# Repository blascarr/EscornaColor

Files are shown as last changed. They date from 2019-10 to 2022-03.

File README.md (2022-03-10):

# EscornaColor
Version de Escornabot con sensor de color **TCS3200**.

El **sensor de color TCS3200** añade formatos de juego interesantes al famoso modelo de [**Escornabot**](https://escornabot.com/web/es).

Para usar el sensor de color, es necesario sustituir la pieza del alojamiento para la canica con el siguiente [modelo STL](https://www.thingiverse.com/thing:3934783) publicado en [Thingiverse](https://www.thingiverse.com/thing:3934783).

<p align="center">
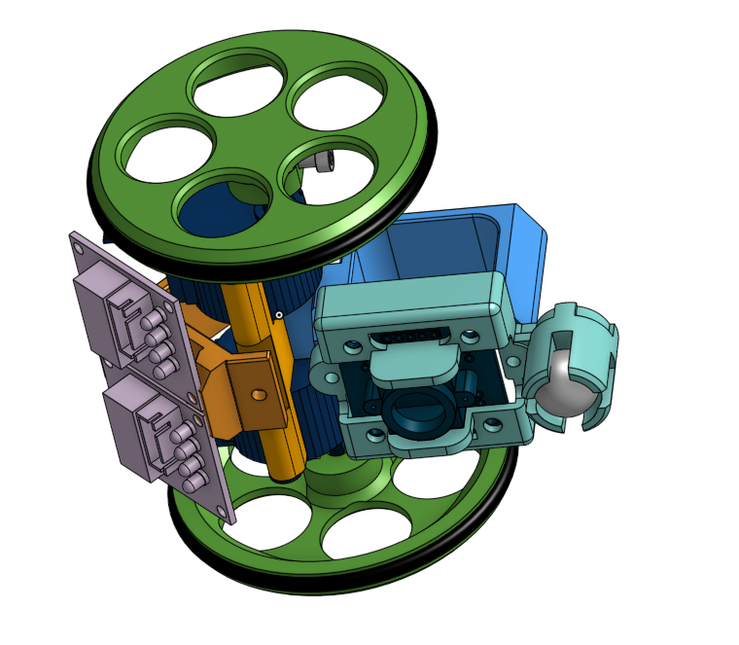
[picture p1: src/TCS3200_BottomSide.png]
	
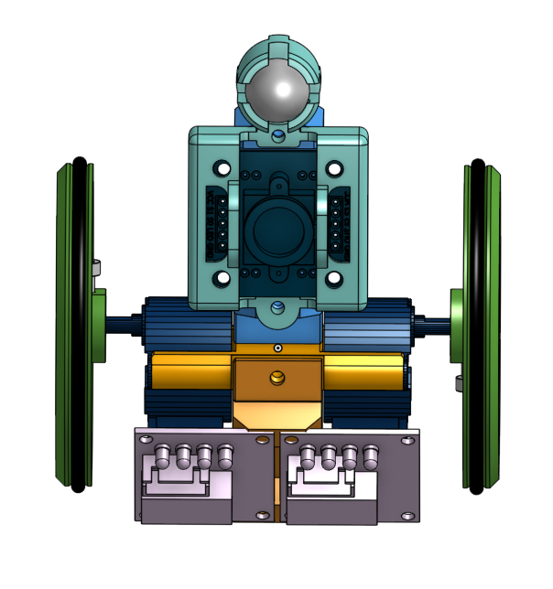
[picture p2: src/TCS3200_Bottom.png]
	
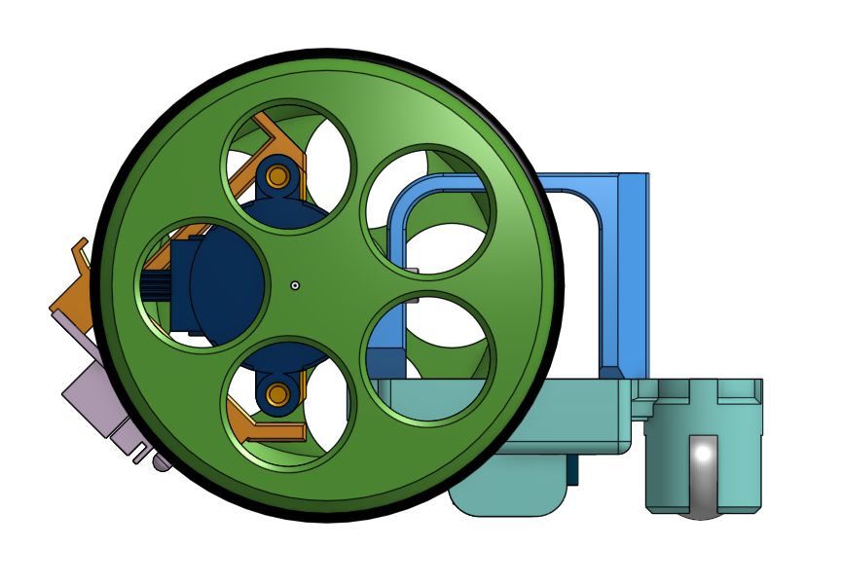
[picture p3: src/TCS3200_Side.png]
	
</p>

El sensor tiene distintos pines, de los cuales los más importantes son el pin S2, S3 y OUT. El pin de LED nos servirá solamente para encender y apagar el módulo.
- S2 --> D11
- S3 --> D12
- OUT --> D13
- LED --> A6
- S0 --> VCC
- S1 --> VCC

Este sensor de color viene preparado para reconocer **8 colores** por defecto que son:

- BLANCO
- NEGRO
- ROJO
- VERDE
- AZUL
- AMARILLO
- NARANJA
- MARRON

# Programa tu EscornaColor.

Para desarrollar una programación personalizada de tu EscornaColor, solo tienes que registrar una función a cada movimiento y **programar tu robot con tus propias reglas**.

Te dejamos unos códigos de ejemplo para que puedas crear tu propio modelo de programación.

Existen dos funciones en caso de ganar ( **win()** ) y en caso de perder el juego ( **game_over()** ).
Puedes crear un modelo de juego en el que puedes perder vidas en función del color que el **EscornaColor** ha detectado. Si el **EscornaColor** llega al color objetivo sin perder todas las vidas ganas.
```cpp
Bot ESCORNABOT;
int lives = 2;

void red(){
  ESCORNABOT.win();
}

void green(){
  lives -= 1;
  Serial.print("Lives: ");Serial.println(lives);
  if (lives <= 0 ){
    ESCORNABOT.game_over();
    Serial.println("GAME OVER");
  }
}
```

También puedes programar los movimientos en función del color que has encontrado con la función **move( )**. Dentro del parámetro de esta función puedes definir los siguientes tipos de movimiento.

- MOVE_NONE
- MOVE_FORWARD
- MOVE_RIGHT
- MOVE_BACKWARD
- MOVE_LEFT
- MOVE_PAUSE
- MOVE_ALT_RIGHT
- MOVE_ALT_LEFT

```cpp
void white(){
  ESCORNABOT.move( MOVE_BACKWARD );
  Serial.println("COLOR White");
}

void black(){
  ESCORNABOT.move( MOVE_FORWARD );
  Serial.println("COLOR Black");
}
```
Ten cuidado, porque puedes caer facilmente en un bucle de movimientos si no piensas bien la secuencia.

Una vez finalizadas tus reglas de juego, deberás asociar una accion de color a cada color en el **setup** de tu programa. El bucle loop se encargará de todo-

```cpp
void setup()
{
    ESCORNABOT.init();
    ESCORNABOT.load_colortable();

    //Color Actions Define
    ESCORNABOT.color_action( WHITE , white );
    ESCORNABOT.color_action( BLACK , black );
    ESCORNABOT.color_action( RED , red );
    
    //GREEN change non consecutively
    ESCORNABOT.color_action( GREEN , green, true );
    //YELLOW need to change from consecutive yellow colors
    ESCORNABOT.color_action( YELLOW , yellow );
    
    //random movements for Blue color
    randomSeed(analogRead(5));
    ESCORNABOT.color_action( BLUE , blue );

    //Brown and Orange not working
    ESCORNABOT.color_action( BROWN , aux_void );
    ESCORNABOT.color_action( ORANGE , aux_void );
}

void loop()
{
    ESCORNABOT.loop();
}

//Auxiliar void function for every color action defined
void aux_void(){
  
}
```

Al final, solo tienes que cargar el código a tu robot y dejarlo funcionar con los objetivos que te has definido.

**IMPORTANTE:** Ten cuidado de no saturar la memoria. Si superas más del 85% de la memoria RAM pueden ocurrir errores, pero puedes jugártela. 

# Formatos de juego a desarrollar.

- [x] El **EscornaColor** tiene un número de vidas limitado. Los colores pueden quitar vidas. El objetivo es llegar vivo al objetivo.
- [ ] Cuando se alcanza un color, se ejecutan las acciones de movimiento hasta llegar al objetivo. Juego de la hormiga. [Hormiga de Langton Simplificado](https://es.wikipedia.org/wiki/Hormiga_de_Langton)

- [ ] A través de una aplicación se pueden ver los colores y movimientos del Escornabot. Sin mirar el tablero ni al EscornaColor hay que dibujar el tablero original.

- [ ] Programación libre de escornabot con distintas dinámicas en base a las lecturas del sensor de color.

El sensor de color requiere de una **calibración inicial** para poder clasificar los colores correctamente. 

# [Calibración del sensor de color TCS3200](http://blascarr.com/lessons/tcs3200-color-sensor-calibration/)

El **Escornacolor** está configurado por defecto para cargar la calibración almacenada en la **EEPROM** manteniendo presionado el botón delantero.

De la misma forma, el **Escornacolor** realizará una calibración manteniendo presionado el botón trasero.

Para realizar esta calibración hay que acceder al puerto serie y escribir un caracter **Y** o **N** para que vaya realizando calibraciones.
En cada calibración nos preguntarán si queremos guardar nuestra tabla de colores en la **EEPROM**. 

Esta calibración se puede realizar a través del **monitor serie** o por **Bluetooth** a través de una aplicación.

### Calibración de intensidades BLANCO - NEGRO
Primero hay que calibrar las lecturas con respecto el color negro **BLACK CALIBRATION** y al color blanco **WHITE CALIBRATION**, que establecen los límites de lectura del sensor. Esta calibración es muy importante para la calibración de nuestra **tabla de colores**. 

### Calibración de la **tabla de colores**
Acto seguido se requiere de una calibración de una tabla de **8 colores** que se almacenan en la **memoria EEPROM**.

Los dos primeros colores son el color **Blanco** y el color **Negro**, y las lecturas deben corresponder a los valores RGB **( 255, 255, 255 )** y **( 0, 0, 0 )** respectivamente.

El resto de colores será una combinación de estos valores RGB. 
**NOTA:** Los valores RGB de cada color debida a la calibración no tienen por qué corresponder exactamente con los valores RGB del color. Esta calibración es una aproximación para cada medida.

# Añade más colores a tu EscornaColor

WORK IN PROGRESS.

Se pueden añadir más colores, pero para ello, hay que tener en cuenta que exista una variación notable en las lecturas para colores .
Recomendamos utilizar variantes de colores facilmente diferenciables, ya que tonos similares pueden dar lugar a errores.

Por ejemplo, el blanco y el amarillo son muy similares. Si la lectura se hace en un punto medio entre dos colores, el resultado puedes ser indeterminado.

Esta extensión se basa en el desarrollo de una librería para módulos **TCS3200** accesible en el siguiente [enlace](https://github.com/blascarr/TCS3200-ColorSensor).

- Puedes aprender más sobre el color en esta [Introducción al color en robótica](http://blascarr.com/lessons/introduccion-al-color/)

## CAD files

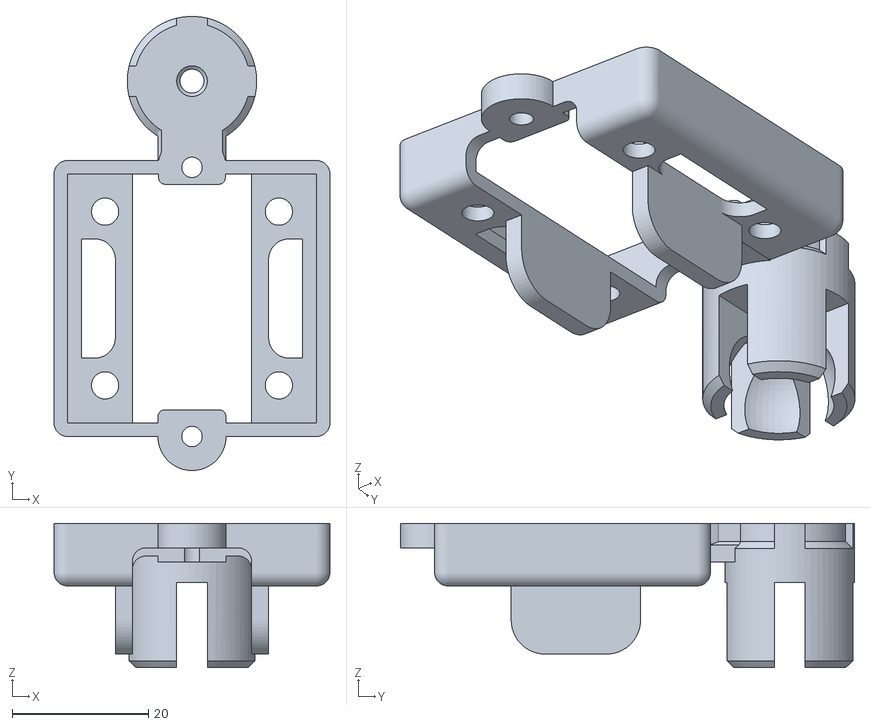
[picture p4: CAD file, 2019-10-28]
STL/ColorSensor_Escornabot.stl
40.5 x 66.6 x 21.2

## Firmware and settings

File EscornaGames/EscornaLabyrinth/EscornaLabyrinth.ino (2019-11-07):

// Escornabot.ino

#include "Bot.h"

//////////////////////////////////////////////////////////////////////
/*
  Reglas del juego.

  Nuestro robot debe ir desde la casilla de color naranja, hasta la casilla de color Verde.
  Pero el tablero aún no está construido completamente. 
  Solo hay unas cuantas casillas que son las trampas que deberemos evitar.
  El resto de colores tienen programados diferentes movimientos.
  Nuestra misión es descubrir que movimiento se corresponde con cada color para llegar desde la salida hasta la meta de forma directa.

  Os dejamos un ejemplo de tablero 

  ////////////////////////////////////////////////////
  |       |       |       |       |       |       |
  |       |       |       |       |       |       |
  |       |       |       |       |       |       |
  ////////////////////////////////////////////////////
  |       |       |       |       |       |       |
  |       |       |   R   |       |   R   |   V   | (META)
  |       |       |       |       |       |       |
  ////////////////////////////////////////////////////  
  |       |       |       |       |       |       |
  |       |   R   |       |       |   R   |       |
  |       |       |       |       |       |       |
  ////////////////////////////////////////////////////
  |       |       |       |       |       |       |
  |SALIDA |       |       |       |       |       |
  |       |       |       |       |       |       |
  ////////////////////////////////////////////////////
  /
*/

Bot ESCORNABOT;
int lives = 4;


void leftforward(){
  ESCORNABOT.move( MOVE_FORWARD );
  ESCORNABOT.move( MOVE_LEFT );
  Serial.println("LEFT - FORWARD");
}

void rightforward(){
  ESCORNABOT.move( MOVE_BACKWARD );
  ESCORNABOT.move( MOVE_RIGHT );
  Serial.println("LEFT - RIGHT");
}

void forward(){
  ESCORNABOT.move( MOVE_FORWARD );
  Serial.println("FORWARD");
}

void winner(){
  ESCORNABOT.win();
  Serial.println(" YOU WIN ");
}

void randomMove(){
    ESCORNABOT.move( random( 8 ) );
    Serial.println(" RANDOM MOVE ");
}

void warning(){
    damage();
    randomMove();
    
}

void damage(){
  lives -= 1;
  Serial.print("Lives: ");Serial.println(lives);
  if (lives <= 0 ){
    ESCORNABOT.game_over();
    Serial.println("GAME OVER");
  }
}
void yellow(){
 
}


//////////////////////////////////////////////////////////////////////

void setup()
{
    ESCORNABOT.init();
    ESCORNABOT.load_colortable();

    //Color Actions Define
    ESCORNABOT.color_action( WHITE , forward );
    ESCORNABOT.color_action( BLACK , rightforward);
    ESCORNABOT.color_action( RED , damage );
    
    //GREEN change non consecutively
    ESCORNABOT.color_action( GREEN , winner );
    //YELLOW need to change from consecutive yellow colors
    ESCORNABOT.color_action( YELLOW , yellow );
    
    randomSeed(analogRead(A5));
    ESCORNABOT.color_action( BLUE , leftforward );

    ESCORNABOT.color_action( BROWN , randomMove);
    ESCORNABOT.color_action( ORANGE , aux_void);
}

//////////////////////////////////////////////////////////////////////

void loop()
{
    ESCORNABOT.loop();
}


void aux_void(){
  
}
//////////////////////////////////////////////////////////////////////


// EOF

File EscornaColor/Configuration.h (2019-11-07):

// Configuration.h
/*

Copyright (C) 2014-2019 Escornabot - http://escornabot.com

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
See LICENSE.txt for details

*/

#ifndef _CONFIGURATION_H
#define _CONFIGURATION_H


//////////////////////////////////////////////////////////////////////
///// general configuration
//////////////////////////////////////////////////////////////////////

// engine to use
#define ENGINE_TYPE_STEPPERS

// button set to use (analog input, digital input)
#define BUTTONS_ANALOG
//#define BUTTONS_DIGITAL

// milliseconds after a button is considered as pressed
#define BUTTON_MIN_PRESSED 30

// milliseconds after a button is considered as long pressed
#define BUTTON_LONG_PRESSED 1000

// put to false to add movements to the program after its execution
#define PROGRAM_RESET_ALWAYS true

// store configuration and program within internal EEPROM
#define USE_PERSISTENT_MEMORY false

// memory capacity for program movements
#define MOVE_LIMIT 100

// milliseconds for the "pause" movement
#define PAUSE_MOVE_MILLIS 1000

// milliseconds delay before starting to move
#define DELAY_BEFORE_GO 500

// milliseconds to pause after every movement
#define AFTER_MOVEMENT_PAUSE 0

// point of view set when Vacalourabot is started
#define POV_INITIAL    POV_CHILD

// bluetooth serial
#define USE_BLUETOOTH false
#define BLUETOOTH_BAUDS 9600

// buzzer
#define USE_BUZZER true
#define BUZZER_PIN 10
#define PROGRAM_FINISHED_RTTL RTTL_FIDO
#define TONE_FREQ_UP 2637
#define TONE_FREQ_RIGHT 4434
#define TONE_FREQ_DOWN 3520
#define TONE_FREQ_LEFT 2217

// simple led
#define USE_SIMPLE_LED false
#define SIMPLE_LED_PIN 13

// keypad leds
#define USE_KEYPAD_LEDS true
#define KEYPAD_LED_PIN_UP A0
#define KEYPAD_LED_PIN_RIGHT A1
#define KEYPAD_LED_PIN_DOWN A2
#define KEYPAD_LED_PIN_LEFT A3
#define KEYPAD_LED_PIN_GO 13

// Color Sensor
#define USE_COLORSENSOR true


//////////////////////////////////////////////////////////////////////
///// Steppers engine setup
//////////////////////////////////////////////////////////////////////

#ifdef ENGINE_TYPE_STEPPERS

// stepper pin setup (digital outputs)
#define STEPPERS_MOTOR_RIGHT_IN1 5
#define STEPPERS_MOTOR_RIGHT_IN2 4
#define STEPPERS_MOTOR_RIGHT_IN3 3
#define STEPPERS_MOTOR_RIGHT_IN4 2
#define STEPPERS_MOTOR_LEFT_IN1 9
#define STEPPERS_MOTOR_LEFT_IN2 8
#define STEPPERS_MOTOR_LEFT_IN3 7
#define STEPPERS_MOTOR_LEFT_IN4 6

// step calibration
#define STEPPERS_STEPS_PER_SECOND 1000
#define STEPPERS_LINE_STEPS 1738
#define STEPPERS_TURN_STEPS 1024

#endif



//////////////////////////////////////////////////////////////////////
///// Button set digital
//////////////////////////////////////////////////////////////////////

#ifdef BUTTONS_DIGITAL

// keypad pin setup (digital or analog inputs) (use 255 if key doesn't exist)
#define BS_DIGITAL_UP A0
#define BS_DIGITAL_RIGHT A1
#define BS_DIGITAL_DOWN A2
#define BS_DIGITAL_LEFT A3
#define BS_DIGITAL_GO A4
#define BS_DIGITAL_RESET 255

#endif // BUTTONS_DIGITAL



//////////////////////////////////////////////////////////////////////
///// Button set analog
//////////////////////////////////////////////////////////////////////

#ifdef BUTTONS_ANALOG

#define BS_ANALOG_WIRES 2
//#define BS_ANALOG_WIRES 3

// keypad pin setup (analog input)
#define BS_ANALOG_PIN A7

// input values for each key pressed (0 if key doesn't exist)
#define BS_ANALOG_VALUE_UP 512
#define BS_ANALOG_VALUE_RIGHT 683
#define BS_ANALOG_VALUE_DOWN 769
#define BS_ANALOG_VALUE_LEFT 860
#define BS_ANALOG_VALUE_GO 810
#define BS_ANALOG_VALUE_RESET 0

#endif // BUTTONS_ANALOG



//////////////////////////////////////////////////////////////////////
///// Button set Bluetooth
//////////////////////////////////////////////////////////////////////

#ifdef USE_BLUETOOTH

// Arduino serial port (default is Serial, use Serial1 with Arduino Micro)
#define BLUETOOTH_SERIAL    Serial
//#define BLUETOOTH_SERIAL    Serial1
//#define BLUETOOTH_SERIAL    Serial2
//#define BLUETOOTH_SERIAL    Serial3

#endif // USE_BLUETOOTH

//////////////////////////////////////////////////////////////////////
///// TCS3200 COLOR Sensor
//////////////////////////////////////////////////////////////////////

#ifdef USE_COLORSENSOR

// Arduino Pins EEPROM
//#define TCS_S0  //VCC
//#define TCS_S1  //VCC

#define TCS_S2   11
#define TCS_S3   12
#define TCS_OUT  13
#define TCS_LED  A6

#define TCS_SAMPLES  40
#define TCS_REFRESH  200
#define TCS_EEPROM 0

#endif // USE_COLORSENSOR


//////////////////////////////////////////////////////////////////////
//////////////////////////////////////////////////////////////////////


#endif // _CONFIGURATION_H

// EOF

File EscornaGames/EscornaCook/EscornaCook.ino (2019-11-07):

// EscornaCook.ino
#include "Bot.h"

/*REGLAS
Sacamos una carta y nos ha tocado un tipo de comida.  

Por ejemplo, la Pizza requiere de los siguientes ingredientes:
  - 0 Bandeja Horno - Negra
  - 1 Harina - Naranja
  - 2 Agua - Azul
  - 3 Verdura - Verde
  - 4 Queso - Amarillo

El objetivo es buscar cada uno de los ingredientes asociados a los colores en orden para hacer nuestra comida para poder cocinarlo. 
Para ejecutar los movimientos, debemos tirar un dado y solo podremos introducir una secuencia de movimientos con el número del dado hasta acercarnos en orden a los colores.

  Cuando se hayan conseguido todos los ingredientes, nos podremos dirigir a la cocina para preparar nuestra comida en el horno.
  
  - END Cocinar - Rojo

  El primero que llegue gana
*/

Bot ESCORNABOT;

bool ingredients[5];

void getIngredient(int n ){
  if( !ingredients[n] ){
    ingredients[n] = true;
    ESCORNABOT.tick_tone();
  }
}

void horno(){
  getIngredient(0);
  if(ingredients[0] == true ){
    Serial.println("Horno");
  }
}

void harina(){
  if(ingredients[0] == true ){
    getIngredient(1);
    Serial.println("Harina");
  }
  
}

void agua(){
  if(ingredients[1] == true ){
    getIngredient(2);
     Serial.println("Agua");
  }
 
}

void verdura(){
  if(ingredients[2] == true ){
    getIngredient(3);
    Serial.println("Verdura");
  }
  
}

void queso(){
  if(ingredients[3] == true ){
    getIngredient(4);
    Serial.println("Queso");
  }
  
}

void cocinar(){
  bool checkingredients = false;
  for(int i = 0; i <= 5 ; i++){
    checkingredients &= ingredients[i];
    if( checkingredients == false ){
      break;
    }
  }
  if( checkingredients ){
    ESCORNABOT.win();
    Serial.println("WIN");
  }
}

//////////////////////////////////////////////////////////////////////

void setup()
{
    ESCORNABOT.init();
    ESCORNABOT.load_colortable();

    //Color Actions Define
    
    ESCORNABOT.color_action( BLACK , horno );
    ESCORNABOT.color_action( RED , cocinar );
    ESCORNABOT.color_action( ORANGE , harina );
    ESCORNABOT.color_action( GREEN , verdura );
    ESCORNABOT.color_action( YELLOW , queso );
    ESCORNABOT.color_action( BLUE , agua );

    //Brown and White not working
    ESCORNABOT.color_action( WHITE , aux_void );
    ESCORNABOT.color_action( BROWN , aux_void );
    
}

//////////////////////////////////////////////////////////////////////

void loop()
{
    ESCORNABOT.loop();
}


void aux_void(){
  
}
//////////////////////////////////////////////////////////////////////


// EOF

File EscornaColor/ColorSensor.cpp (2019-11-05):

// ColorSensor.h
//ZGZMakerSpace - Blascarr Contribution
/*

Copyright (C) 2014-2019 Escornabot - http://escornabot.com

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
See LICENSE.txt for details
*/

#include "EventManager.h"
#include "ColorSensor.h"

#define SERIAL_DEBUG
#define SERIALDEBUG Serial

//Pattern for DEBUG detection
#ifndef DEBUG_STARTCMD 
	#define  DEBUG_STARTCMD "{" 
#endif
#ifndef DEBUG_ENDCMD 
	#define  DEBUG_ENDCMD "}"
#endif
#ifndef DEBUG_SEPCM 
	#define  DEBUG_SEPCMD ","
#endif

//Pattern for CALIBRATION detection
#ifndef CAL_STARTCMD 
	#define  CAL_STARTCMD "<"
#endif
#ifndef CAL_ENDCMD
	#define  CAL_ENDCMD ">"
#endif
#ifndef CAL_SEPCMD
	#define  CAL_SEPCMD "|"
#endif

//Pattern for COLOR detection
#ifndef COLOR_STARTCMD 
	#define  COLOR_STARTCMD "#"
#endif
#ifndef COLOR_ENDCMD 
	#define  COLOR_ENDCMD "*"
#endif

#if defined(SERIAL_DEBUG)
	#define  DUMP(s, v)  { SERIALDEBUG.print(F(s)); SERIALDEBUG.print(v); }
	#define  DUMP_CMD(s, v)  { SERIALDEBUG.print(DEBUG_STARTCMD); SERIALDEBUG.print(F(s)); SERIALDEBUG.print(v); SERIALDEBUG.print(DEBUG_ENDCMD); }
	#define  DUMPS(s)    {  SERIALDEBUG.print(F(s)); }
	#define  DUMPS_CMD(s)    { SERIALDEBUG.print(DEBUG_STARTCMD); SERIALDEBUG.print(F(s)); SERIALDEBUG.print(DEBUG_ENDCMD);}
	#define  DUMPPRINTLN() { SERIALDEBUG.println();}

	#define  DUMPCAL(s, v)  { SERIALDEBUG.print(CAL_STARTCMD); SERIALDEBUG.print(F(s)); SERIALDEBUG.print(v);SERIALDEBUG.print(CAL_ENDCMD); }
	#define  DUMPSCAL(s)    { SERIALDEBUG.print(CAL_STARTCMD); SERIALDEBUG.print(F(s)); SERIALDEBUG.print(CAL_ENDCMD); }
	#define  DUMPDEBUGCAL(s, v)  { DUMPCAL(s, v); }
	#define  DUMPSDEBUGCAL(s)    { DUMPSCAL(s); }
	#define  DUMPSAVAILABLE()    SERIALDEBUG.available()
	#define  DUMPCOLOR(code) { SERIALDEBUG.print(COLOR_STARTCMD);SERIALDEBUG.print(code);SERIALDEBUG.print(COLOR_ENDCMD);}
	#define  DUMPREADSTRING() {SERIALDEBUG.readString();}
	#define  DUMPREAD(str) { str = SERIALDEBUG.read();}
#else
	#define  DUMP(s, v)
	#define  DUMP_CMD(s, v) 
	#define  DUMPS(s)
	#define  DUMPS_CMD(s)
	#define  DUMPPRINTLN() 
	#define  DUMPCAL(s, v)
	#define  DUMPSCAL(s)
	#define  DUMPDEBUGCAL(s, v)
	#define  DUMPSDEBUGCAL(s)
	#define  DUMPSAVAILABLE() false
	#define  DUMPCOLOR(code)
	#define  DUMPREADSTRING()
	#define  DUMPREAD(str)
#endif
//////////////////////////////////////////////////////////////////////

extern EventManager* EVENTS;

//////////////////////////////////////////////////////////////////////

/**
 * \Color Sensor TCS3200 for color detection.
 * \author @blascarr
 */

ColorSensor::ColorSensor(const Config* config)
{
    this->_config = config;
    _isON = true;
}

void ColorSensor::init()
{	
	EVENTS->add(this);
	ColorSensor::setPins( _config->pin_S2 , _config->pin_S3, _config->pin_OUT, _config->pin_led );
	ColorSensor::nSamples( _config->nSamples  );
	ColorSensor::setRefreshTime( _config->refreshTime );
	ColorSensor::setFrequency( TCS3200_FREQ_HI );
	ColorSensor::LEDON( true );
}

//////////////////////////// Event Habdling //////////////////////////////////////////

void  ColorSensor::moveExecuted ( MOVE move ){
	
	ColorSensor::read();
	int cli= ColorSensor::checkColor( &_rgb );

	if ( COLORACTION [ cli ].onChange ){
		//Accion cuando encuentra nuevo color 
		if(cli != ColorSensor::_lastColor){
			ColorSensor::_lastColor = cli;
			COLORACTION [ getColorID() ].action();
		};
		//if ( onChangeColor() ){
			
		//};
	}else{	
		//Accion ejecutada siempre que finaliza un movimiento
		ColorSensor::readColor();
		COLORACTION [ getColorID() ].action();
	}
	DUMPCOLOR( ColorSensor::getColor() );

}


void  ColorSensor::buttonLongReleased(BUTTON button){
	if ( button == BUTTON_DOWN){
		ColorSensor::calibration(0);
	}

	if ( button == BUTTON_UP){
		ColorSensor::loadCal(0);
	}

	if ( button == BUTTON_LEFT){
		ColorSensor::readColor();

		//Serial.print( ColorSensor::getColor() );
		DUMPCOLOR( ColorSensor::getColor() );
	}
}

//////////////////////////////////////////////////////////////////////

void ColorSensor::setPins(uint8_t S2, uint8_t S3, uint8_t OUT, uint8_t LED ){ 
	ColorSensor::_S2 = S2; ColorSensor::_S3 = S3; ColorSensor::_OUT = OUT; ColorSensor::_LED = LED; 
	pinMode( ColorSensor::_S2, OUTPUT);
	pinMode( ColorSensor::_S3, OUTPUT);
	pinMode( ColorSensor::_LED, OUTPUT);
	pinMode( ColorSensor::_OUT, INPUT);
};

void  ColorSensor::setRefreshTime(unsigned long refreshTime){
	ColorSensor::refreshTime = refreshTime;
}

void  ColorSensor::setEEPROMaddress( uint16_t nEEPROM ){
	ColorSensor::_nEEPROM = nEEPROM;
}

void  ColorSensor::LEDON(bool ledON){
	digitalWrite(_LED, (ledON) ? HIGH : LOW );
	ColorSensor::_isON = ledON;
}

void  ColorSensor::setID(String ID){
	ID.toCharArray(ColorSensor::_ID, TCS_SIZENAME);
}

void ColorSensor::setFrequency( uint8_t f ){
	ColorSensor::_freqSet = f;
	/* set the sensor Frequency 
		|	Freq 	|	S0 		|	S1 		|
		|	OFF 	|	LOW 	|	LOW 	|
		|	LOW 	|	LOW 	|	HIGH 	|
		|	MEDIUM 	|	HIGH 	|	LOW 	|
		|	HIGH 	|	HIGH 	|	HIGH 	|
	*/
	switch (f){
		case TCS3200_FREQ_HI:  /*DUMPS("HI");*/  digitalWrite(_S0, HIGH);  digitalWrite(_S1, HIGH);  break;
		case TCS3200_FREQ_MID: /*DUMPS("MID");*/ digitalWrite(_S0, HIGH);  digitalWrite(_S1, LOW);   break;
		case TCS3200_FREQ_LO:  /*DUMPS("LO");*/  digitalWrite(_S0, LOW);   digitalWrite(_S1, HIGH);  break;
		case TCS3200_FREQ_OFF: /*DUMPS("OFF");*/ digitalWrite(_S0, LOW);   digitalWrite(_S1, LOW);   break;
		//default:  DUMP("Unknown freq option", f); break;
	}
}

void ColorSensor::setFilter(uint8_t f){
	/* set the sensor color filter 
		|	RGB 	|	S2 		|	S3 		|
		|	R 		|	LOW 	|	LOW 	|
		|	G 		|	HIGH 	|	HIGH 	|
		|	B 		|	LOW 	|	HIGH 	|
		|	X 		|	HIGH 	|	LOW 	|
	*/

	switch (f){
		case TCS3200_RGB_R:   digitalWrite(_S2, LOW);   digitalWrite(_S3, LOW);   break;
		case TCS3200_RGB_G:   digitalWrite(_S2, HIGH);  digitalWrite(_S3, HIGH);  break;
		case TCS3200_RGB_B:   digitalWrite(_S2, LOW);   digitalWrite(_S3, HIGH);  break;
		case TCS3200_RGB_X:   digitalWrite(_S2, HIGH);  digitalWrite(_S3, LOW);   break;
		//default:  DUMP("Unknown filter option", f); break;
	}
}


/*
	-------------------------------------------------------
	------------Non - Blocking Functions-------------------
	-------------------------------------------------------
*/

void ColorSensor::read() {
	ColorSensor::currentMillis = millis();
	if(ColorSensor::currentMillis-ColorSensor::oldMillis >= ColorSensor::refreshTime){
		ColorSensor::LEDON(true);
		ColorSensor::readRGB();
		ColorSensor::LEDON(false);
		ColorSensor::oldMillis  = ColorSensor::currentMillis;

	}
}

bool ColorSensor::onChangeColor(){
	if ( ColorSensor::_isON  ){
		ColorSensor::read();
		int cli= ColorSensor::checkColor( &_rgb );

		if(cli != ColorSensor::_lastColor){

			ColorSensor::_lastColor = cli;
			#if SENDCOLOR 
				DUMPCOLOR( readColor() );
			#endif

			return true;
		}else{
			return false;
		}
	}else{
		return false;
	}

}

void ColorSensor::readColor(){
	ColorSensor::read();
	int cli= ColorSensor::checkColor( &_rgb );
	ColorSensor::_lastColor = cli;
}
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

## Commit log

2019-10-28 EscornaColor Project
    [Configuration.h]
2019-10-28 README and STL
    [ColorSensor_Escornabot.stl]
2019-10-28 Events added ButtonPressed - MoveExecuted and buttonLongReleased for Calibration (Non continuous )
    [Configuration.h]
2019-10-28 EEPROM Configuration calibration for loading in init method
    [Configuration.h]
2019-10-29 Calibration Bluetooth Prepared
    [Configuration.h]
2019-11-02 Color Game mode
    [Configuration.h]
2019-11-02 Fixed color actions. External programming . BE CAREFUL with void reference for every color
    [ColorSensor.cpp, EscornaColor.ino]
2019-11-02 README for programming and calibration
2019-11-05 Reviewed Calibration and programmable model
2019-11-07 Set POV CHILD
    [Configuration.h]

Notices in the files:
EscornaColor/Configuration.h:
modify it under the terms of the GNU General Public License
